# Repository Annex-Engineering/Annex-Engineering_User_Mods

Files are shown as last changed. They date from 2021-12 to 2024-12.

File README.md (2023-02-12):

# Annex Engineering - User Mods

This repo hosts mods created by the development team and end users of the Annex Engineering line of printers, extruders and other misc projects. Please follow the folder hierarchy described below when creating a pull request

This repo may also host mods created for other printers, by the annex development team. They are filed in the "Printers/Other_Printers" folder

## Folder Hierarchy:
 -  / printer / user_name-mod_name / STLs /
 -  / printer / user_name-mod_name / CAD /
 -  / printer / user_name-mod_name / Images /
 -  / printer / user_name-mod_name / README.md

### Notes: 
 - README.md should include any pictures, boms, instructions, etc
 - CAD should include all steps, parasolids, solidworks files, or other cad files
 - STLs should include any and all STLs required
 - Images should include all required pictures, videos, etc

Our discord server can be found here: 

Join me on Discord (https://discord.gg/MzTR3zE)

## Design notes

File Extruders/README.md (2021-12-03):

# Annex Engineering - User Mods - Extruders

This repo hosts mods created by end users of the Annex Engineering line of Extruders. Please follow the folder hierarchy described on the main README.md when creating a pull request

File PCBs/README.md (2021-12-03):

# Annex Engineering - User Mods - PCBs

This repo hosts mods created by end users of the Annex Engineering line of PCBs. Please follow the folder hierarchy described on the main README.md when creating a pull request

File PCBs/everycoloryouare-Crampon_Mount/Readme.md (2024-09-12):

# Nozzle Mount for Crampon

A Crampon mount that attaches to the hotend and positions the accelerometer at the nozzle tip position. The standard Crampon mount provided on the [Annex Engineering PCB GitHub](https://github.com/Annex-Engineering/Annex_Engineering_PCBs/tree/master/crampon/Clampon_Mounting_Bracket/) is too wide to fit between the part cooling fans on a K3 and has the accelerometer offset from the nozzle. This version fixes those issues.

Two versions for the bottom printed part are available for USB cables with 6mm and 8mm thick housing on the connector.

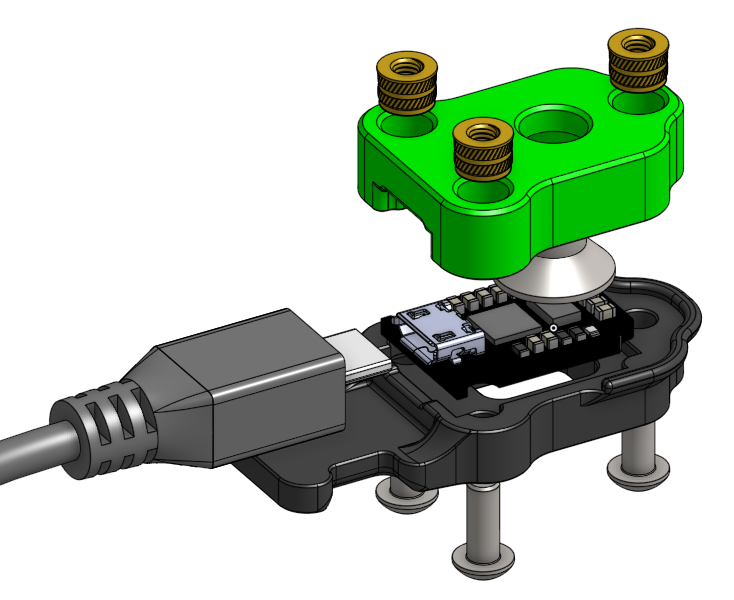
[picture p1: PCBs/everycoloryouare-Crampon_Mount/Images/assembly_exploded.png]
Exploded


## Goals

- Positions the ADXL345 accelerometer at the nozzle tip
- Minimizes weight while still being easy to install (work in progress)
- Fits on the K3 carriage without hitting the part cooling fan ducts or Beacon probe
- Works with 6mm and 8mm thick USB cables

## BOM

- Sources for all items can be found in the Annex [sourcing guide](https://docs.google.com/spreadsheets/d/1O3eyVuQ6M4F03MJSDs4Z71_XyNjXL5HFTZr1jsaAtRc/htmlview#) for the K3 or at the official Annex Stores ([US](https://store.annex.engineering/), [EU](https://annex-engineering.eu/))

| Item | Qty Required |
| --- | --- |
| Crampon PCB | 1 |
| M6 x 10mm or 12mm Flat Head (included with Crampon) | 1 |
| M3 x 8mm SHCS or BHCS | 3 |
| M3 x 5mm Dia x 4mm Length Heat Set Insert | 3 |
| Micro USB Cable with 6mm or 8mm thick housing | 1 |
| Cable Tie | 1 |

## Notes

Relative position of ADXL345 chip (highlighted) and nozzle mounting bolt:

| This Version | Standard | Legacy (Minimal) |
| --- | --- | --- |
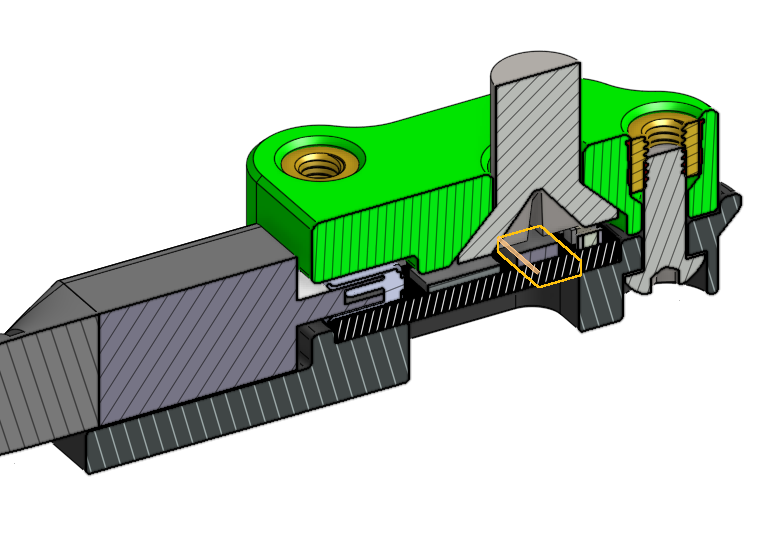
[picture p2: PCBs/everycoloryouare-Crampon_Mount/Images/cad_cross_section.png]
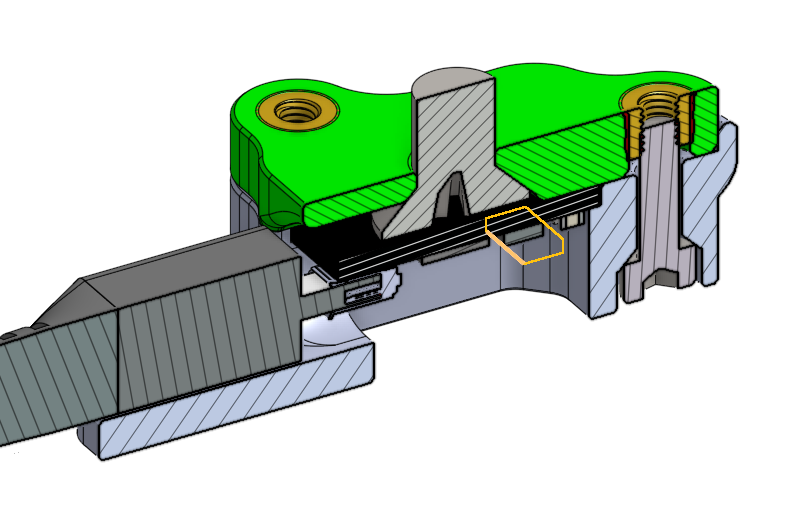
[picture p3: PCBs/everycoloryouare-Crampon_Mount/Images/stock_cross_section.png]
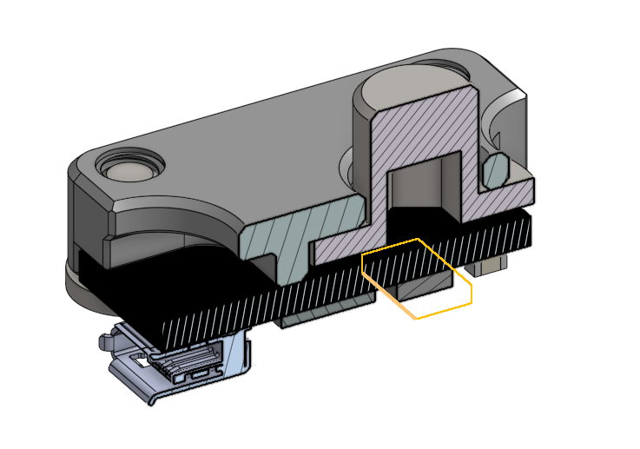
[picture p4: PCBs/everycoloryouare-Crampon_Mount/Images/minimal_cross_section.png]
|  |  |  |

- The PCB recess in the bottom printed part is 1.4mm, so the Crampon should sit 0.2 above the lip so that it is in contact with the top printed part.

## Assembly

1. Insert three M3 heat set inserts into the top printed part.
2. Insert Crampon PCB into the bottom printed part.
3. Attach USB cable to Crampon and zip-tie USB cable to the strain relief tab on the bottom printed part.
4. Remove nozzle from the hotend.
5. Attach the top printed part into the hotend thread using a M8 flat head bolt.
6. Attach the bottom printed part using three M3 bolts.

## Print Settings

- Nozzle Size: 0.4mm or 0.5mm
- Material: ABS, ASA, or PLA
- Layer Height: 0.2mm
- Infill Percentage: 40%
- Wall Count: 4
- Solid Top/Bottom Layers: 5

Print with imported orientation and no shrink compensation for ABS, ASA, or PLA.

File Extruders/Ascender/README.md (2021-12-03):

# Annex Engineering - User Mods - Extruder - Ascender

This repo hosts mods created by end users of the Annex Engineering - Ascender Extruder. Please follow the folder hierarchy described on the main README.md when creating a pull request

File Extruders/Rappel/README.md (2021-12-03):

# Annex Engineering - User Mods - Extruder - Rappel

This repo hosts mods created by end users of the Annex Engineering - Rappel Extruder. Please follow the folder hierarchy described on the main README.md when creating a pull request

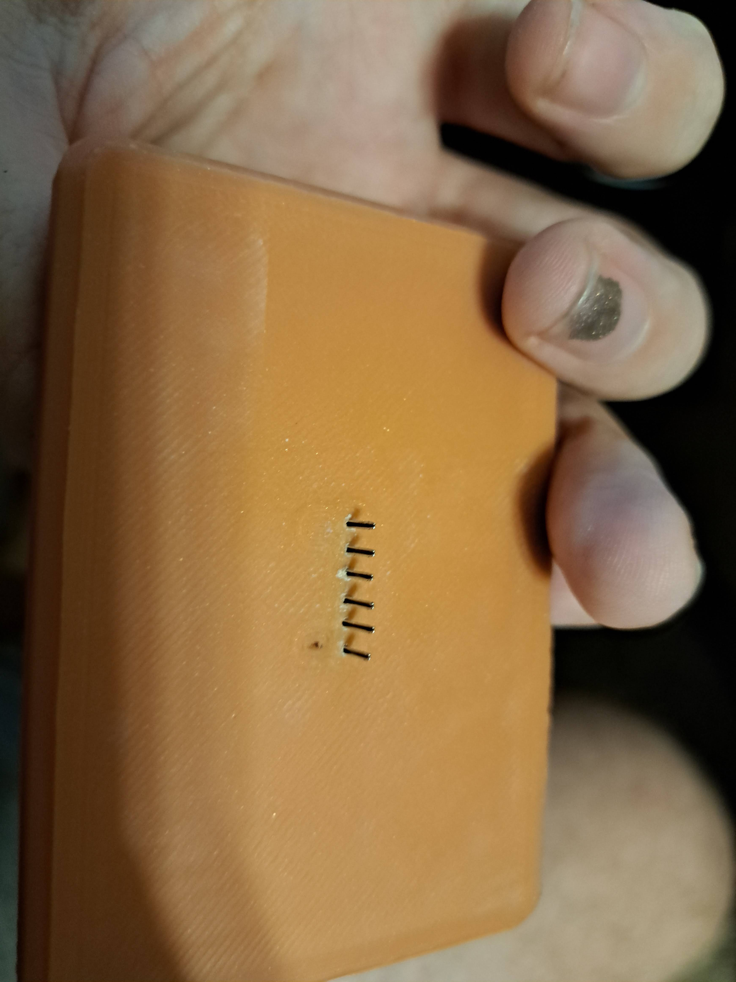
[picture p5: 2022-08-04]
Printers/K3/kirby-ADXL-headers-electronics-box-panel/Images/Front.jpg

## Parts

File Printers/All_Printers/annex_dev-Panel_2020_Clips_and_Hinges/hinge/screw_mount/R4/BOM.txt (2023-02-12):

Screw mount hinge BOM (per one hinge):
1x M5x40 SHCS or BHCS
1x M5 nut
2x M3x8 SHCS
2x M3 post assembly nut or T-nut
2x F695 bearing

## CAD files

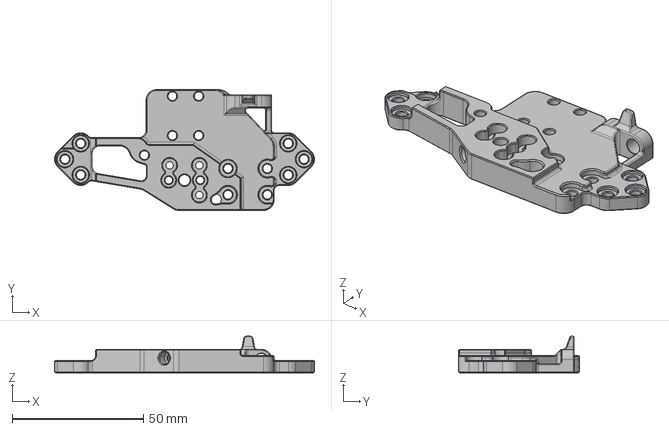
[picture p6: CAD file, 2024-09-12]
Printers/K3/everycoloryouare-K3rabiner_Micro_Plate/CAD/k3rabiner_sherpa_micro_mosqito_dragon_main_body_x1_rev2.step
99.0 x 46.0 x 13.9 mm

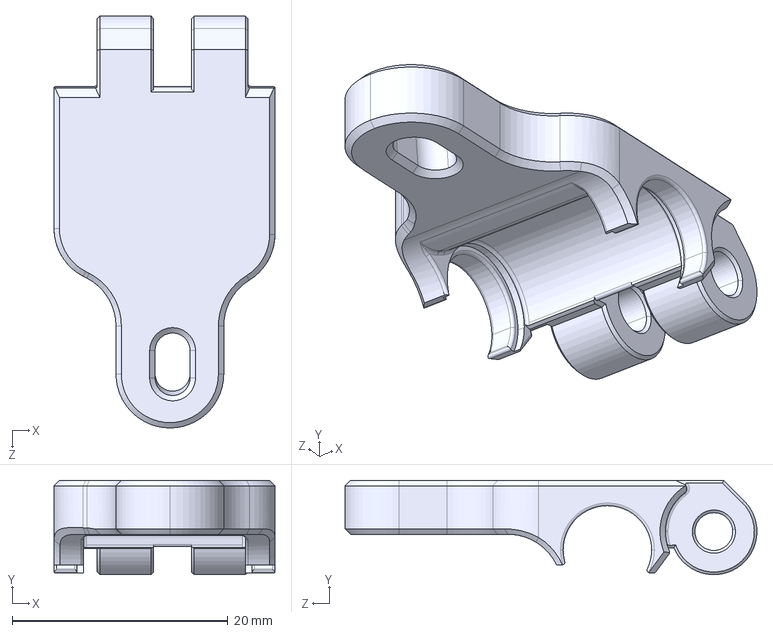
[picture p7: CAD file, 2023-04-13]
Extruders/Ascender/churls-Ball_bearing_latch/CAD/mr85_ascender_latch.STEP
20.5 x 8.74 x 38.2 mm

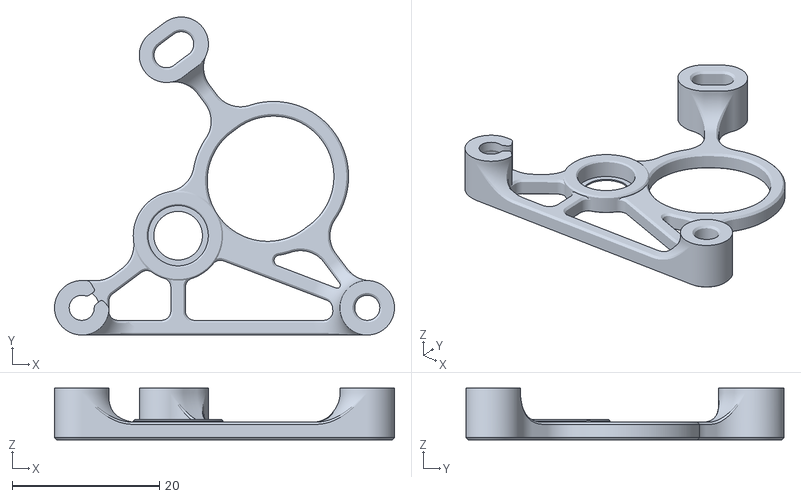
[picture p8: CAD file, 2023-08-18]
Extruders/Sherpa_Micro/Extruder_Mods/Churls_Fixed_Idler_Micro/STLs/Bondtech RIDGA V2/Sherpa_micro_housing_rear_0.2LH.STL
46.2 x 43.2 x 7.00

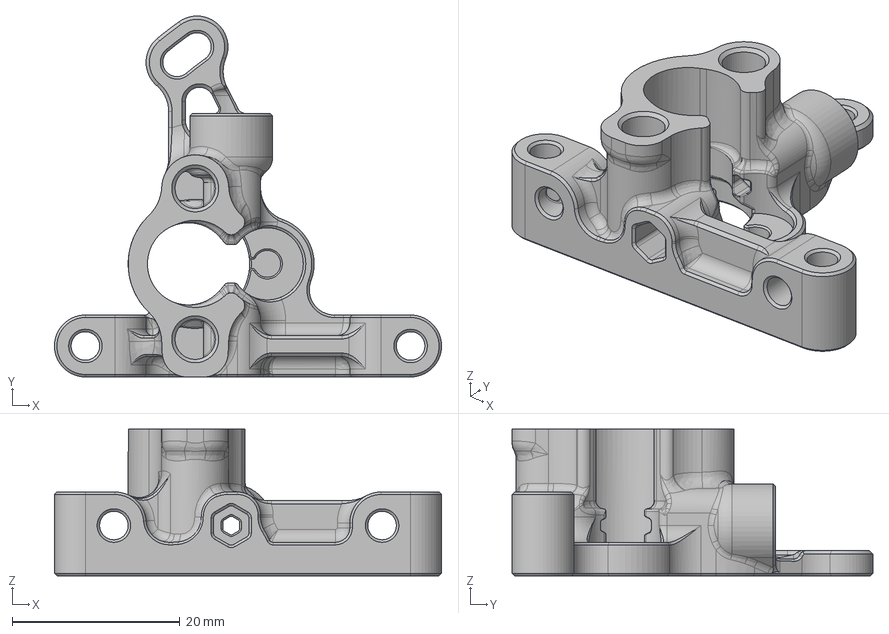
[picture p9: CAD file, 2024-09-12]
Extruders/Sherpa_Micro/Extruder_Mods/everycoloryouare-Fixed_Idler_Micro_and_Collet/CAD/fixed_idler_housing_core_collet_x1_rev2.step
46.2 x 43.1 x 17.5 mm

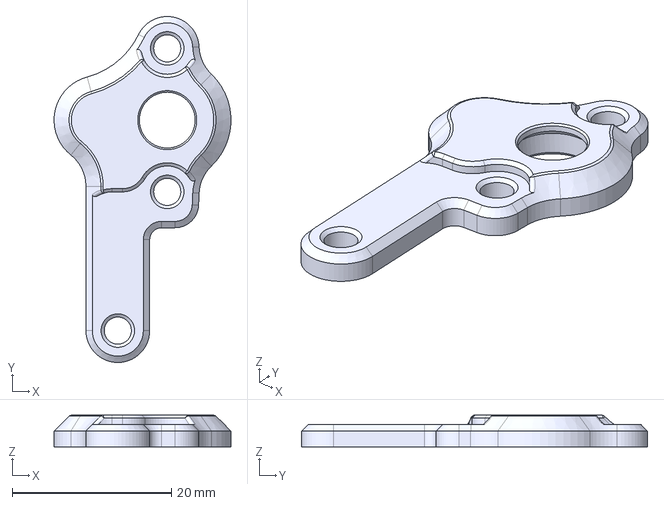
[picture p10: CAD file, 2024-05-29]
Extruders/Sherpa_Micro/Extruder_Mods/everycoloryouare-Fixed_Idler_Micro_and_Collet/CAD/mirrored/fixed_idiler_housing_front_k_mirrored_x1_rev1.step
22.2 x 43.4 x 4.00 mm

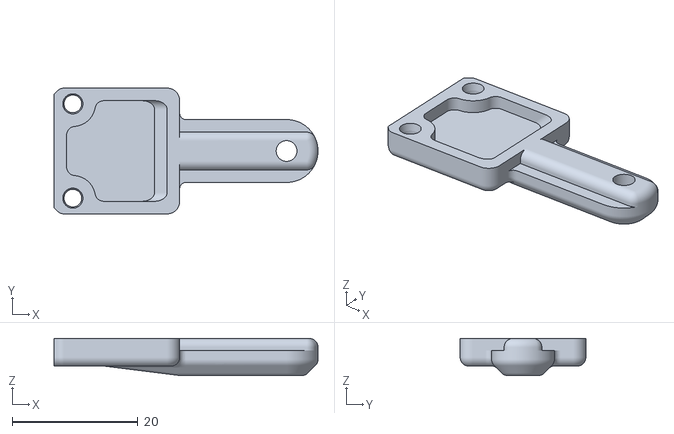
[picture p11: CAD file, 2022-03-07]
Extruders/Sherpa_Micro/Toolheads/Churls-Micro_Stiffy_E3/STLs/Optional/x_endstop_holder.STL
42.0 x 20.0 x 5.90

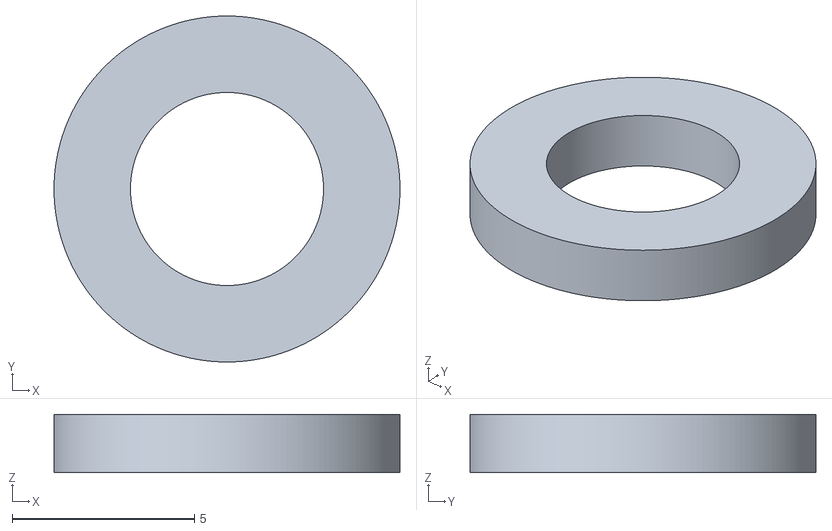
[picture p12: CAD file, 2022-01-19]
Extruders/Sherpa_Micro/Toolheads/Churls-Micro_Stiffy_E3/STLs/V_Roller_Spacer.STL
9.50 x 9.50 x 1.60

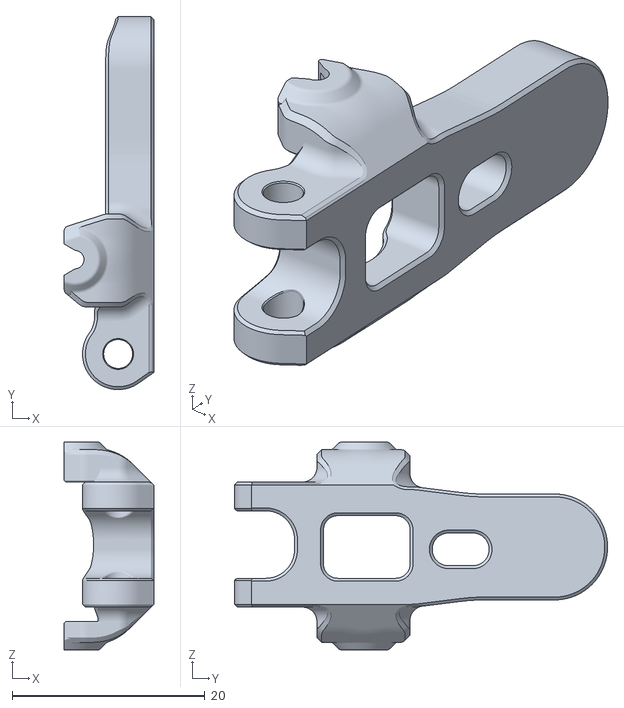
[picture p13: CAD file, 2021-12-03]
Extruders/Sherpa_Mini/Extruder_Mods/alch3my-4.6mm_mod/stls/sherpa_mini_release1 parts - idler_arm_long^housing_sherpa_mini_a3_r9c.stl
9.30 x 38.8 x 21.6

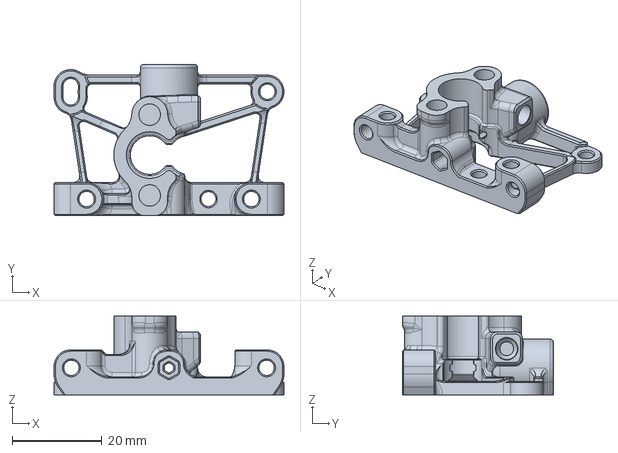
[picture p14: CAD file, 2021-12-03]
Extruders/Sherpa_Mini/Extruder_Mods/alch3my-Housing_Core_with_ECAS_coupler/housing_core_ECAS.step
51.2 x 33.7 x 17.5 mm

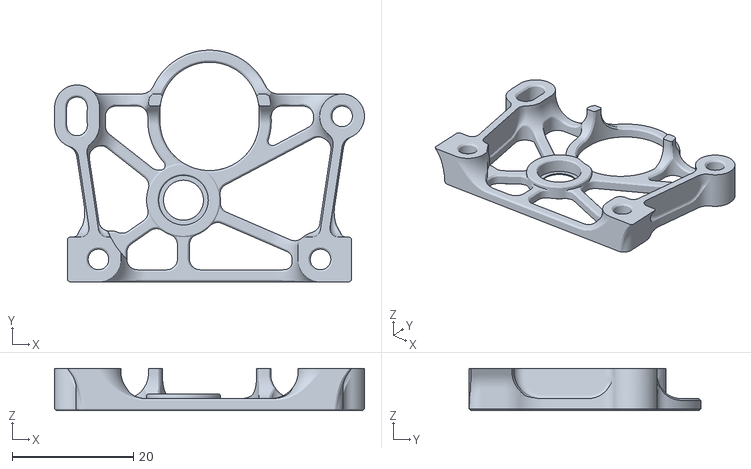
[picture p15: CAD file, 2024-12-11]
Extruders/Sherpa_Mini/Extruder_Mods/ChadwickTheCrab-4.6mm_Mod R2/STLs/housing_rear_nema14^housing_sherpa_mini_a3_r17_FDM.stl
51.2 x 38.3 x 7.00

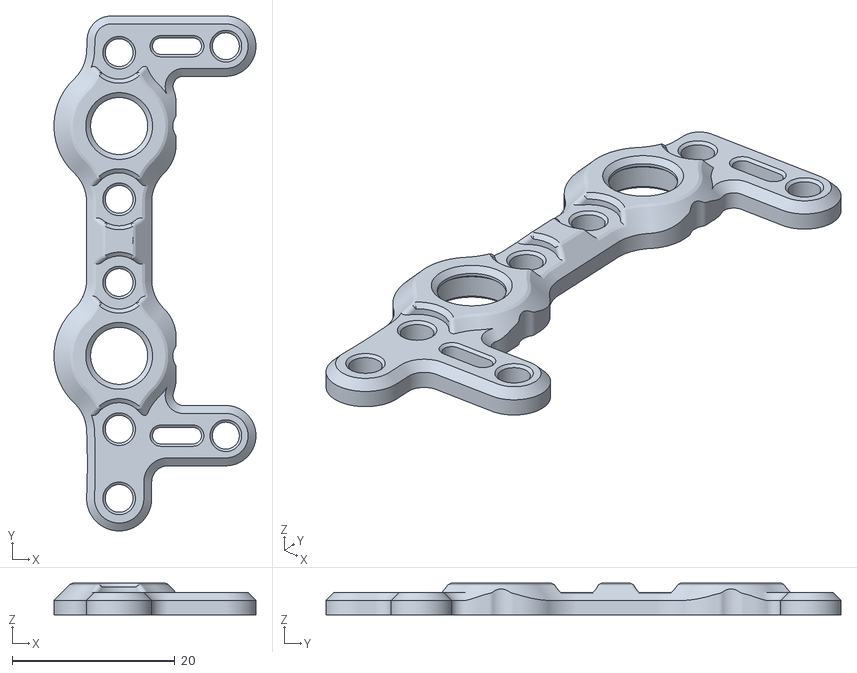
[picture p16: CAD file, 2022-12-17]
Extruders/Sherpa_Mini/Extruder_Mods/Churls-Double_Sherpa_Mini/STLs/housing_front_k.STL
24.8 x 63.2 x 3.90

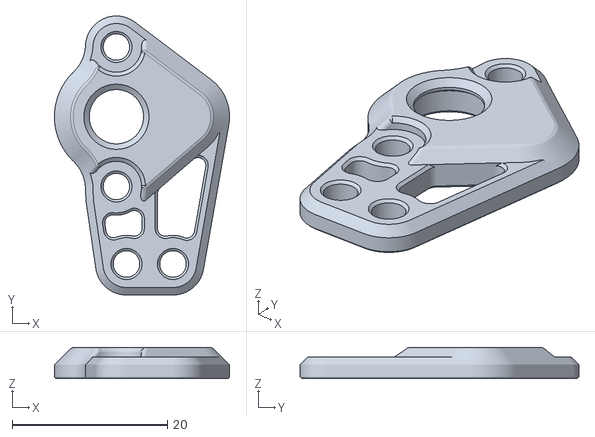
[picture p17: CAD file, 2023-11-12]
Extruders/Sherpa_Mini/Extruder_Mods/Churls-Fixed_Idler_Mini/STLs/Bondtech Gears/fixed_idler_housing_front_k2.STL
22.6 x 36.0 x 4.00

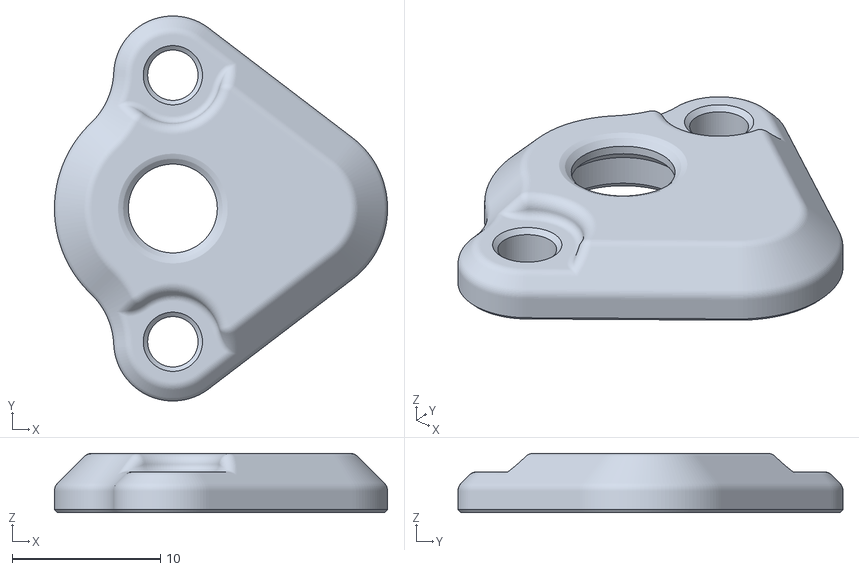
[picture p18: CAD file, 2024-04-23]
Extruders/Sherpa_Mini/Extruder_Mods/Churls-Fixed_Idler_Mini/STLs/Bondtech Gears/RIDGA V1/fixed_idler_mini_housing_front_btRIDGA.stl
22.5 x 26.0 x 4.00

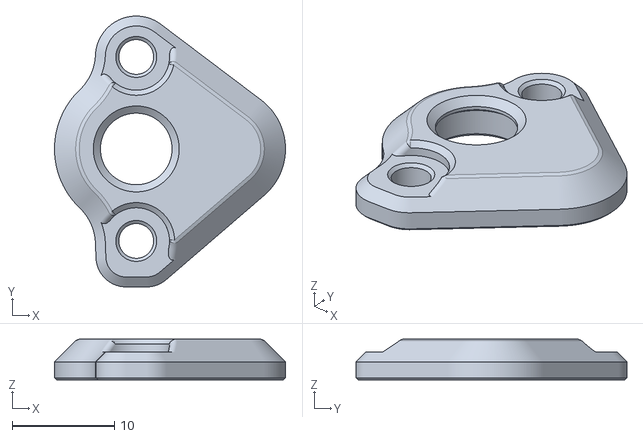
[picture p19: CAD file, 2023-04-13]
Extruders/Sherpa_Mini/Extruder_Mods/Churls-Fixed_Idler_Mini/STLs/Mellow vzRIDGA Gears/Sherpa_Housing_front.STL
22.6 x 26.5 x 4.00

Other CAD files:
Extruders/Sherpa_Micro/Extruder_Mods/everycoloryouare-Fixed_Idler_Micro_and_Collet/STLs/mirrored/[a]_fixed_idler_housing front_k_mirrored_x1_rev1.stl
Extruders/Sherpa_Mini/Extruder_Mods/Churls-Mini_RIDGA/STLs/Bondtech RIDGA Gears/RIDGA V1/4x7x2.5 Bearings/RIDGA_Sherpa_housing_front_4x7x2.5_BRG.STL
Extruders/Sherpa_Mini/Extruder_Mods/Churls-Mini_RIDGA/STLs/Bondtech RIDGA Gears/RIDGA V1/4x8x3 Bearings/RIDGA_sherpa_mini_housing_front_4x8x3_BRG.STL
Extruders/Sherpa_Micro/Extruder_Mods/Churls_Fixed_Idler_Micro/STLs/Bondtech RIDGA V1/Sherpa_micro_housing_front.STL
Extruders/Sherpa_Micro/Extruder_Mods/Churls_Fixed_Idler_Micro/STLs/Bondtech RIDGA V1/Sherpa_micro_housing_rear.STL
Extruders/Sherpa_Micro/Extruder_Mods/Churls_Fixed_Idler_Micro/STLs/Bondtech RIDGA V2/Sherpa_housing_front.STL
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

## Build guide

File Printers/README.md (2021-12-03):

# Annex Engineering - User Mods - Printers

This repo hosts mods created by end users of the Annex Engineering line of printers. Please follow the folder hierarchy described on the main README.md when creating a pull request

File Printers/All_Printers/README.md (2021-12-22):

# Annex Engineering - User Mods - Printer - Any ANNEX Engineering Printer

This repo hosts mods created by end users of Annex Engineering printers. Please follow the folder hierarchy described on the main README.md when creating a pull request

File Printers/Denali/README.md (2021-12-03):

# Annex Engineering - User Mods - Printer - Denali

This repo hosts mods created by end users of the Annex Engineering - Denali Printer. Please follow the folder hierarchy described on the main README.md when creating a pull request

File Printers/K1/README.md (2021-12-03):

# Annex Engineering - User Mods - Printer - K1

This repo hosts mods created by end users of the Annex Engineering - K1 Printer. Please follow the folder hierarchy described on the main README.md when creating a pull request

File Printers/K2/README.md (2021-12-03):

# Annex Engineering - User Mods - Printer - K2

This repo hosts mods created by end users of the Annex Engineering - K2 Printer. Please follow the folder hierarchy described on the main README.md when creating a pull request

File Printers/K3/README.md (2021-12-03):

# Annex Engineering - User Mods - Printer - K3

This repo hosts mods created by end users of the Annex Engineering - K3 Printer. Please follow the folder hierarchy described on the main README.md when creating a pull request

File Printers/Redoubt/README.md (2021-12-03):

# Annex Engineering - User Mods - Printer - Redoubt

This repo hosts mods created by end users of the Annex Engineering - Redoubt Printer. Please follow the folder hierarchy described on the main README.md when creating a pull request

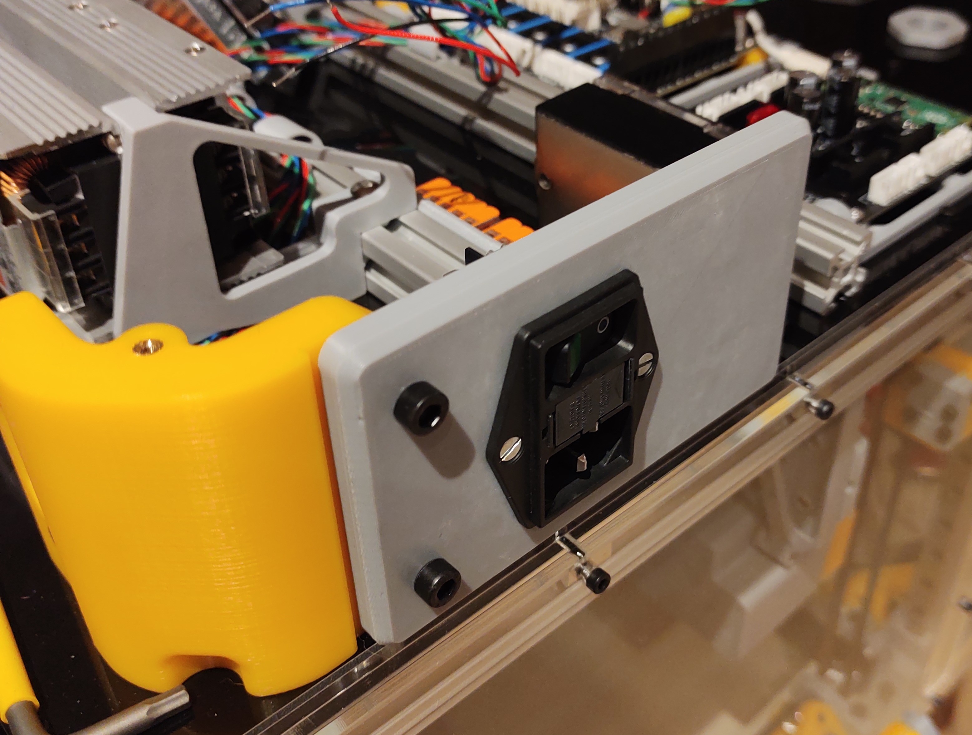
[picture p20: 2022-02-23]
Printers/All_Printers/Pringineer-Ebox_Plate_Schurter_DD11/Images/Schurter_Inlet_DD11_front.jpg

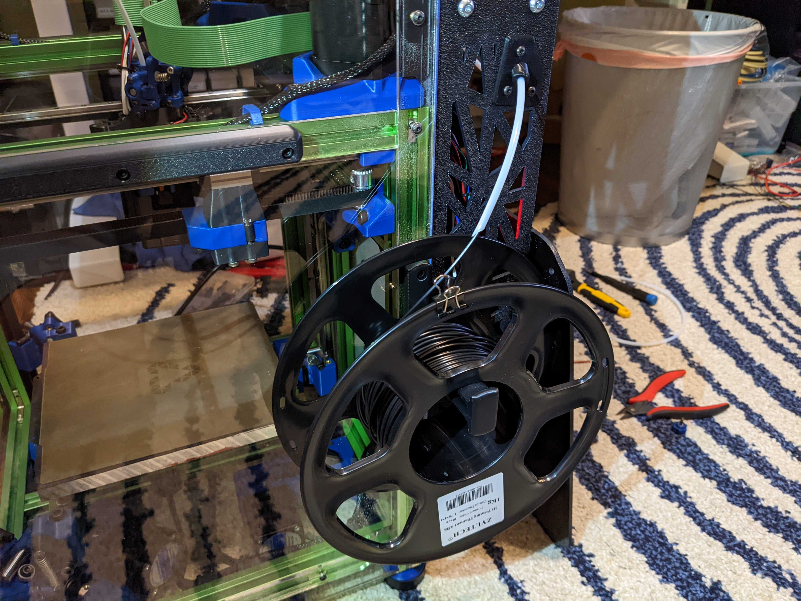
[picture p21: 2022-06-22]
Printers/K3/long-right_side_PTFE_tube_guide/Images/sideview.jpg

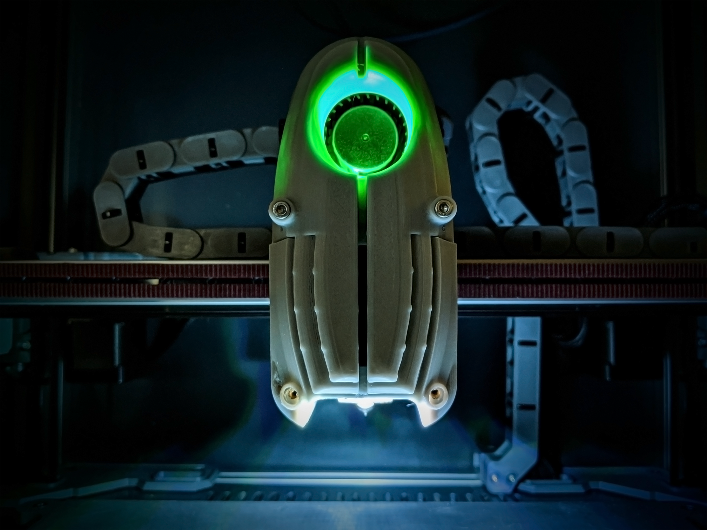
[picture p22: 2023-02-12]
Printers/Non_Annex_Printers/VORON_Printers/VORON_Afterburner_Beta1/annex_dev-(M)ORON_Afterburner_Front_Cover/Images/Action.png

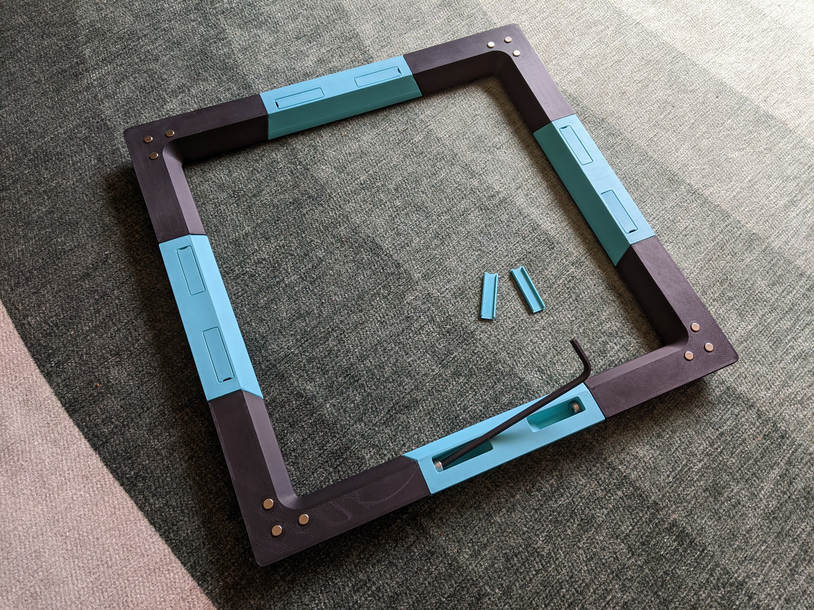
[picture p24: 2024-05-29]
Printers/K3/everycoloryouare-M5_Tophat/Images/printed_bottom.jpg

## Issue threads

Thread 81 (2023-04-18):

housing front version without 5th screw

Horstelin, 2023-04-18:
Hey, could you design/upload a version of the housing_front(double) that does not have the additional mounting hole? The current version is not compatible with the dragon burner and other toolheads.

Otherwise: great design!

Closed 2023-10-07.

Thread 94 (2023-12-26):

Potentially out of date STL or incorrect readme for 2.4 reinforced gantry

sqwoobler, 2023-12-26:
The readme for v3 of the reinforced gantry shows a heat set insert in the z tensioner (to remove the spacer when stuck),  the space for this insert seems to be missing from the STL (below). Not sure if this is a mistake in documentation and the design changed, or perhaps a STL was not updated with the readme.

https://github.com/Annex-Engineering/Annex-Engineering_User_Mods/blob/6e3e89a6c8ef50cbd4bdfff7f6232c564b06ec55/Printers/Non_Annex_Printers/VORON_Printers/VORON_V2dot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

sqwoobler, 2024-01-05:
Mistake on my end.

Closed 2024-01-05.

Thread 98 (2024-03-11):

Newer revisions of stealthburner x carriage mount are shorter than they should be

KianSajjadi, 2024-03-11:
The 3rd revision of the mount had a change in the mounting height of the beacon causing the rapido nozzle to crash into the bed. Compare these two links with the same rev3 label:
https://github.com/Annex-Engineering/Annex-Engineering_User_Mods/blob/17229e6174104a9cb21d33a0cb7ea2c23882a710/Printers/Non_Annex_Printers/VORON_Printers/VORON_V2dot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
https://github.com/Annex-Engineering/Annex-Engineering_User_Mods/blob/4cb96361011dc72d3039e8c95225dbc5614b5aa5/Printers/Non_Annex_Printers/VORON_Printers/VORON_V2dot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

The first link has the correct beacon mounting height whereas the second link changes the mounting height of the beacon causing nozzle crashes. I think there should be a second version in the STLs where the original mounting height of the beacon is included for rapido users.

Closed 2024-05-29.

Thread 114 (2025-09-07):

Stealthburer Beacon X carriage: offset documentation

system-dsn, 2025-09-07:
Thanks for providing this carriage!

I haven't been able to find a definitive source for the nozzle-to-probe offsets so I went to various CAD models to measure:

- Beacon sensor to "nose" distance: 8.5mm
- "Nose" of Beacon to X carriage hotend mounting surface: 1.0mm
- Stealthburner Revo Voron mount, mounting surface to nozzle: 14.6mm

So the y offset should be 8.5+1.0+14.6=24.1mm.

If my measurements are right then it might be helpful for others to document this in the README:

```
[beacon]
x_offset: 0
y_offset: 24.1
```

(This is only for the Revo Voron with the normal profile Beacon RevH. Not sure about other Beacon/hotend combinations.)

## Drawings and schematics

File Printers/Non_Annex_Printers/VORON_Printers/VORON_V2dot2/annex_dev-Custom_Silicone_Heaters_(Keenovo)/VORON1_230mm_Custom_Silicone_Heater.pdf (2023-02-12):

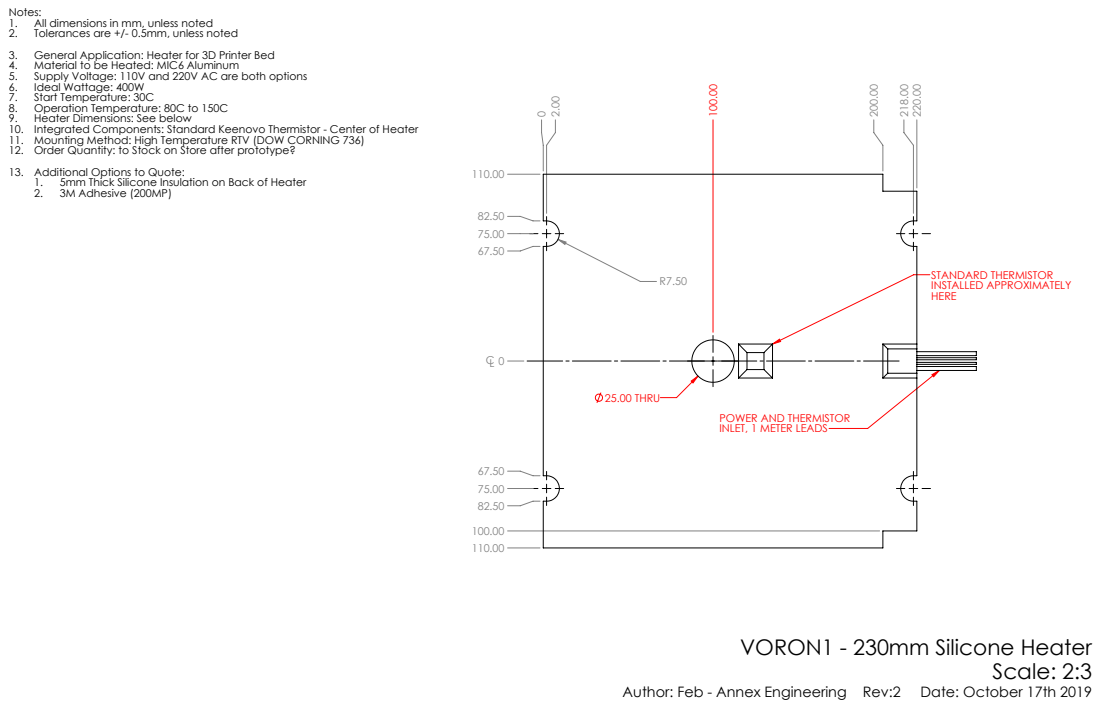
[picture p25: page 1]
25.00 THRU; STANDARD THERMISTOR INSTALLED APPROXIMATELY HERE; VORON1 - 230mm Silicone Heater Scale: 2:3

Notes:
1. All dimensions in mm, unless noted
2. Tolerances are +/- 0.5mm, unless noted
3. General Application: Heater for 3D Printer Bed
4. Material to be Heated: MIC6 Aluminum
5. Supply Voltage: 110V and 220V AC are both options
6. Ideal Wattage: 400W
7. Start Temperature: 30C
8. Operation Temperature: 80C to 150C
9. Heater Dimensions: See below
10. Integrated Components: Standard Keenovo Thermistor - Center of Heater
11. Mounting Method: High Temperature RTV (DOW CORNING 736)
12. Order Quantity: to Stock on Store after prototype?
13. Additional Options to Quote:
1. 5mm Thick Silicone Insulation on Back of Heater
2. 3M Adhesive (200MP)

POWER AND THERMISTOR
INLET, 1 METER LEADS

Author: Feb - Annex Engineering Rev:2 Date: October 17th 2019

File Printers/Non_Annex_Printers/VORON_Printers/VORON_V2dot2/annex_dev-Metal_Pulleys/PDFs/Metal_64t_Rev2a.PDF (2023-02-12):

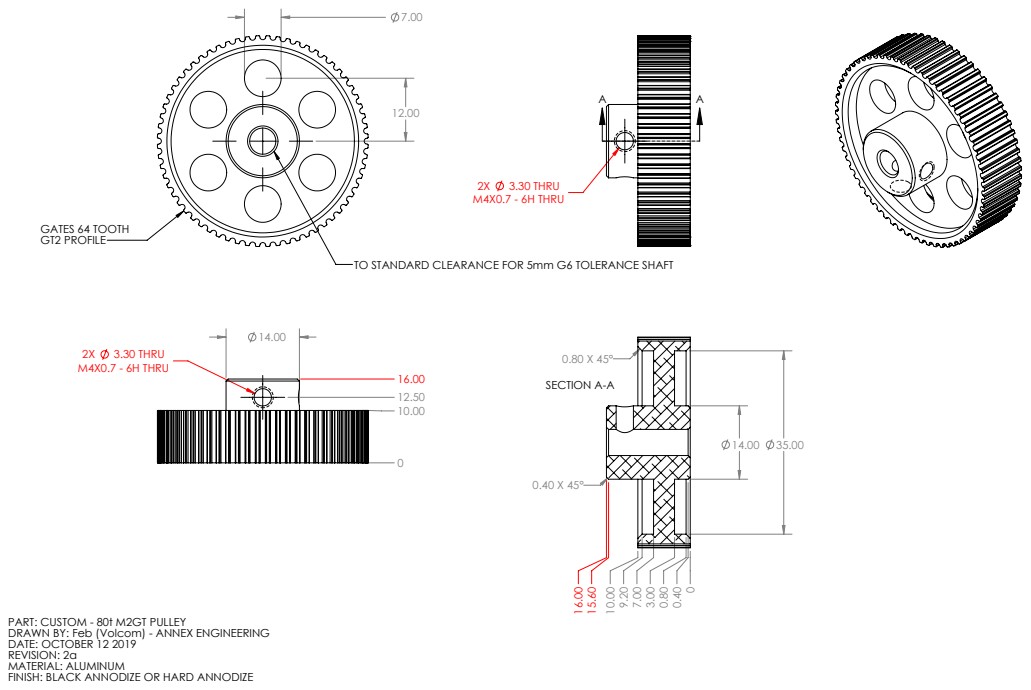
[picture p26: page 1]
GATES 64 TOOTH GT2 PROFILE; 3.30 THRU; M4X0.7 - 6H THRU; SECTION A-A

TO STANDARD CLEARANCE FOR 5mm G6 TOLERANCE SHAFT

PART: CUSTOM - 80t M2GT PULLEY
DRAWN BY: Feb (Volcom) - ANNEX ENGINEERING
DATE: OCTOBER 12 2019
REVISION: 2a
MATERIAL: ALUMINUM
FINISH: BLACK ANNODIZE OR HARD ANNODIZE

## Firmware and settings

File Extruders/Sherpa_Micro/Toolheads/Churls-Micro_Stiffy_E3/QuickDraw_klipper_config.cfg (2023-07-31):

# Download Dalegaard's xz dockable probe module to `~/klipper/klippy/extras/ folder on klipper host as `xz_dockable_probe.py`:
#	A copy of this module has been placed in this repository with Dalegaard's permission. You can download it with these SSH commands:
#		cd ~/klipper/klippy/extras/
#		wget https://raw.githubusercontent.com/churls5495/Annex-Engineering_User_Mods/main/Extruders/Sherpa_Mini/Toolheads/Churls-Stiffy_E3/xz_dockable_probe.py
#		cd ../..
#		echo "klippy/extras/xz_dockable_probe.py" >> .git/info/exclude
#		systemctl restart klipper
#
#	It can also be found here: https://gist.github.com/dalegaard/3f1b8695275a15b1888119304d79b88d
#
#	This module provides additional klipper commands:
#		probe_attach		# attaches probe to toolhead
#		probe_detach		# detaches probe from toolhead
#		probe_lock		# disables auto docking functionality
#		probe_unlock		# reenables auto docking functionality
#		G28 lock_probe=1	# disables auto docking after homing
#		probe_detach force=1	# unlock_probe + probe_detach
#
#	Example:
#		G28 lock_probe=1	# Home XY, attach probe, home Z with probe on bed, hold probe (rather than auto docking immediately as G28 alone would)
#		bed_mesh_calibrate	# generate mesh
#		probe_detach force=1 	# unlocks and docks

# Modifications to printer.cfg
[stepper_z]
endstop_pin: probe:z_virtual_endstop # was ^PC2
#position_endstop: 0.0      	# comment out or delete this line

[stepper_x]
position_max: 265		# more X travel to enable probing along X=225. This is why the upper right v-roller bolt is flipped.

# Additions to printer.cfg
[xz_dockable_probe]
dock_pin: ^PC2			# stock Z endstop pin
dock_x: 17			# X position of nozzle that aligns toolhead and probe magnets
park_delta_x: -15		# X travel to retrieve probe from dock (relative to dock_x)
detach_delta_x: 15		# X travel to detach probe from toolhead (relative to dock_x)
z_hop: 20			# Z travel to clear dock
home_xy_position: 148.5,116.72	# probe point for homing (bed center - probe offset)
#hook_commands: False 		# optional setting to disable the auto attach/detach features. Default is True

[probe]
pin:^PC14			# pin wired to QuickDraw
x_offset: -30
y_offset: 0.78
z_offset: 7.55			# calibrate with probe_calibrate command
samples: 3
sample_retract_dist: 10
samples_result: median
samples_tolerance: 0.01
samples_tolerance_retries: 3
speed: 3
lift_speed: 15

[bed_mesh]
mesh_min: 5,5
mesh_max: 230,230
horizontal_move_z: 10
probe_count: 5,5
fade_start: 0.4
fade_end: 2
bicubic_tension: 0.1
speed: 200
algorithm: bicubic
relative_reference_index: 12

[gcode_macro clear_Z_offset]
description: reset Z offset to zero
gcode:
    SET_GCODE_OFFSET Z=0 

[gcode_macro probe_prep]
description: Heat bed and attach probe
gcode:
    {% set BED_TEMP = params.BED_TEMP|default(60) %}
    M190 S{BED_TEMP}
    G28 lock_probe=1
    
[gcode_macro dock_probe]
gcode:
    probe_detach force=1

[gcode_macro mesh]
description: Heat bed, attach probe, home, mesh, detach probe
gcode:
    {% set BED_TEMP = params.BED_TEMP|default(60) %}
    M190 S{BED_TEMP}
    G28 lock_probe=1
    bed_mesh_calibrate
    probe_detach force=1


[screws_tilt_adjust]
screw1: 236.5,202.5 
screw1_name: rear right 
screw2: 66.5,202.5 
screw2_name: rear left 
screw3: 66.5,32.5
screw3_name: front left
screw4: 236.5,32.5
screw4_name: front right
speed: 200
horizontal_move_z: 10
screw_thread: CW-M4

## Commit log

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2021-12-13 Magprobe for Switchwire MGN12H README
    Update broken images and broken link to the probe housing.
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2022-02-08 raised lowest point of duct tips 1mm.
    ducts were hitting bed before nozzle on some assemblies. this provides more clearance. There should be 0.75mm of clearance on stock setups now.
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2022-02-10 Add K3 Klipper Screen mod
    This adds a door mounted 3.5" KlipperScreen driven display.
    [back_case.stl, front_case.stl, hinge_arm.stl]
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2022-02-10 Corrections to quickdraw cfg
    [QuickDraw_klipper_config.cfg]
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2022-02-10 CAD and Quickdraw updates for Stiffy and Chubby
    - Raised lowest points of stiffy and chubby
    - updated cad with changes
    - added quickdraw documentation to chubby
    [Chubby.x_t, QuickDraw_klipper_config.cfg, Stiffy.x_t]
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2022-02-16 Added 4020 Fan support to Stiffy
    new 4020 fan brace STLs
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2022-02-21 UHP bracket mod
    Modded UHP bracket for dual PSU
    [UHP_mod_bracket (mirrored).stl, UHP_mod_bracket v7.f3d, UHP_mod_bracket v7.step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]
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2022-03-07 updated QD dock STL, added adjustable X endstop
    [x_endstop_holder.STL]
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2022-03-07 Adding QD macros to stiffy and chubby
    [QuickDraw_klipper_config.cfg]
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2022-03-12 Set correct orientation
    [led-profile-mount.stl]
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2022-04-18 Adds Stiffy for Ender-3 V2
    [Stiffy_Ender-3_V2.stl]
2022-04-20 Fix led mount issue with height of certain part
    [led-profile-mount.stl]
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2022-05-25 folder restructuring for e3v2 for stiffy and chubby
    [Chubby_E3V2.stl, Stiffy_E3V2.stl]
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2022-06-18 Stiffy gets Sherpa Micro Version
    [Stiffy_micro.STEP, Stiffy_micro.x_t]
2022-06-19 Created Micro Stiffy Toolhead
    [Micro_Stiffy.x_t, QuickDraw_klipper_config.cfg, V_Roller_Spacer.STL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]
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2022-07-10 Add files via upload
    new models with updated names
    [probe_Body.stl, probe_pin_v3.stl]
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2022-07-11 Add files via upload
    updated to v4. parts going through testing.
    [pin_v4.stl, probe body_v4.stl]
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2022-08-03 Added two mods: ADXL jumper blanking box, and push-fit PTFE connector
    See readmes for each file.
    [Electronics_Box_Blanking_Plate_ADXL_headers.SLDPRT, Electronics_Box_Blanking_Plate_ADXL_headers.STL, Inner_Cap.STL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]
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2022-08-29 OV5640 Camera (100 degree) Mount
    Mount for 100 degree OV5640 Camera that sits in the back right corner.
    [2020_extrusion_cable_cover.stl, OV5640_Mount_StockScrews_10degree.stl, OV5640_Mount_StockScrews_15degree.stl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]
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2022-09-06 Added cable tie post and improved Quickdraw mounting
    [Stiffy_micro.STEP]
2022-09-07 Micro Stiffy Updates
    better QD magnet retention
    cable post
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2022-09-08 Fix Clearances
    [Volcomosq spacer v3.step, Volcomosq_Spacer.stl.3mf]
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2022-09-08 moved stiffy fan braces to optional folder
2022-09-25 Adding Neptune 2 version of the Stiffy
    [Stiffy_Neptune2.step]
2022-10-16 add K3 Waveshare Screen Mount
    Wwavershare 7.9" Screen mount for the K3, based on PRZY's K3+ Mount.
    [LCD_FRAME_K3_STANDARD.stl]
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2022-12-17 updated micro stiffy cad
    [Micro_Stiffy.x_t]
2022-12-17 deleted magnet retention features
    they didn't work.
    [Micro_Stiffy.x_t, Micro_Stiffy_no_post.x_t]
2023-01-13 Metal motor mount for K3
    Modified from released K3 CADS
    [Metal_XY_Motor_Mount.step]
2023-02-03 Chubby - QD simplification
    use glue and run wires down the side of the magnets rather than sandwiching
    [Chubby.x_t]
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2023-03-17 added fixed gear sherpa variants
2023-03-19 Pi Camera V3 Mount for K3 by Long
    [Pi Cam 3 Mount - Lens Cover - 12.4mm Lens.stl, Pi Cam 3 Mount - Mount - 15 degree down.stl, Pi Cam 3 Mount - Mount - 25 degree down.stl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]
2023-03-20 Upload K3 DFA Carabiner mount mod
    Carabiner mount for DFA on a K3 with full clearance
    [K3_DFA_Carabiner_Mount.step, K3_DFA_Carabiner_Mount.stl]
2023-03-24 added sherpa fixed idler CAD
    [RIDGA_Sherpa_Mini_housing_core.STEP, RIDGA_Sherpa_Mini_housing_core.x_t, Sherpa_micro_fixed_idler_housing_core.STEP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]
2023-03-24 added fixed gear housing front CAD
    [Sherpa_fixed_idler_housing_front_k.STEP]
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2023-03-25 added Beacon probe specific K3 nozzle wiper parts
    [Beacon_NozzleWiper.step, Nozzle_Wiper_Arm_Beacon.stl, Nozzle_Wiper_Base_Beacon.stl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]
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2023-03-27 Added ridga and fixed idler CAD
    [RIDGA_Sherpa_Micro_Housing_Core.STEP, RIDGA_Sherpa_Micro_Housing_Core.x_t, RIDGA_Sherpa_Micro_housing_front_k_4x8x3_bearing.STEP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]
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2023-04-01 Create Pi Cam 3 Mount - Lens Cover - 12.0mm Lens.stl
    Add 12.0 mm lens option
    [Pi Cam 3 Mount - Lens Cover - 12.0mm Lens.stl]
2023-04-01 small tweaks to CAD and Readme
    Added 12.0mm lens option in addition to the 12.4mm lens option for the picam v3 mount and updated the CAD.
    Added 2mm spacer for the right sided ptfe tube guide (only for people still on the old ebox).
    [PiCam3 Mount v40.f3d, PiCam3 Mount v40.step, PiCam3 Mount v43.f3d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]
2023-04-02 Move old K3 ebox usermods to Outdated folder
    [Electronics_Box_Blanking_Plate_ADXL_headers.SLDPRT, Electronics_Box_Blanking_Plate_ADXL_headers.STL, Electronics_Box_Blanking_Plate_Combo.step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]
2023-04-02 add Stiffy_E5_Dragonfly_BMS remix
    [Carabiner_mounting_Plate.stl, Stiffy3_E5_Dragonfly_BMS.step, Stiffy3_E5_Dragonfly_BMS.stl]
2023-04-03 Stiffy and Chubby get Beacon mounting
    [Chubby.STEP, Chubby.x_t, Stiffy.x_t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]
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2023-04-08 Added fixed idler sherpas for mellow vzRIDGA gears
    [Sherpa Housing_front.STL, Sherpa_micro_housing_front.STL, Sherpa_micro_housing_rear.STL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]
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2023-04-11 Upload LED Mod and tweak formatting
    Uploading the LED Mod I made for my K3 with tweaked mounts and flush door mount.
    Also fixed formatting in readme in my other mod
    [Diffuser_x3.stl, DoorSealAndLights.step, FrontMountAndDoorSeal.stl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]
2023-04-11 Update LEDHolder_x3.stl
    Fixed exported STL orientation
    [LEDHolder_x3.stl]
2023-04-12 Added Fixed idler Ascender
2023-04-13 Added MR85 fixed idler ascender mod
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2023-05-08 Added latest stiffy CAD
    [QuickDraw_klipper_config.cfg]
2023-06-02 Modified the frostbite duct, everything else is the same.
    [frostbite_duct_horizontal_STEP.step]
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2023-09-02 M5 Tophat Mod
    Added all relevant CAD, STLs, Images, and readme for the M5 tophat mod.
    [[a]_tophat_lid_structure_b_x4_rev1.step, [a]_tophat_lid_structure_c_x8_rev1.step, [a]_tophat_lid_structure_c_x8_rev1.stl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]
2023-09-02 Added Alignment Tools
    Added two alignment tools to the Printer/K3 folder, also fixed some spelling mistakes in the readme of the tophat mod.
    [mgn9c_m8-1.25_adapter_x1_rev1.step, mgn9c_m8-1.25_adapter_x1_rev1.stl, xy_pulley_shim_tool_x1_rev1.step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]
2023-09-04 Added Wago bed mount folder and files
    Also renamed tophat folder using underscore instead dash
    [[a]_tophat_lid_structure_b_x4_rev1.step, [a]_tophat_lid_structure_c_x8_rev1.step, [a]_tophat_lid_structure_c_x8_rev1.stl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]
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2023-09-05 Fixed chamber on carabiner mount top
    also updated images to have 8mm usb version so there is no intersection
    [crampon_mount_top_x1_rev1.step, crampon_mount_top_x1_rev1.stl]
2023-09-05 Fixed orientation of top stl
    [crampon_mount_top_x1_rev1.stl]
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2023-09-07 Fixed crampon mount readme
    Corrected bolt size for flat head screw
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2023-09-27 Added precompensated STLs
    Added 10 more versions of the tophat middle piece so that parts can be printed pre-comensated by different amounts, from 0.1 to 1.0%. Also updated Readme to reflect this change
    [[a]_tophat_lid_structure_b_x4_rev1.step]
2023-11-02 Adding Waveshare 4.3 bezel to mount to ebox
    [Waveshare_4_3_Screen Cover v2.3mf, Waveshare_4_3_Screen Cover v2.f3d]
2023-11-03 Moving to correct folder
    [Waveshare_4_3_Screen Cover v2.3mf, Waveshare_4_3_Screen Cover v2.f3d]
2023-11-03 Lan (CAT5) keystone as a connector for input shaping
    [Keystone Panel Mount v1.f3d, Panel Edge - Lan Keystone v5.3mf]
2023-11-11 Added sherpa mini with fixed idler, ridga, ECAS
    [Sherpa Housing - Sherpa_housing_front-1.STL, fixed_idler_housing_front.STL]
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2023-11-11 added sherpa fixed idler housing front k2
    [Sherpa Housing - Sherpa_housing_front-1.STL, fixed_idler_housing_front.STL, fixed_idler_housing_front_k2.STL]
2023-11-12 Update Beacon Mount
    Moved Beacon .285mm upwards, allowing all hotends to fit within beacons zone of 2.6-3mm from nozzle. Due to the voron revo being .285mm longer in vorons cad.
    [beacon_sb_xcarriage.STEP, x_carriage_left_x1_rev2.STL, x_carriage_left_x1_rev3.stl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]
2023-11-22 now with more hacks, i mean correctness
    [x_carriage_left_x1_rev3.stl, x_carriage_right_x1_rev3.stl]
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2023-12-06 Add inline filament sensor and sherpa mini and micro sensor mods
    [[a]_idler_arm_long_x1_rev1.STL, inline _filament_sensor_(5mm_collet).x_t, inline_filament_sensor_(6mm_collet).x_t]
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2024-02-12 Update Churls fixed Idler Sherpa Mini
    Change the RIDGA V1 to allow the use of the 6t motor. Also changed the body based on RC2
    [fixed_idler_housing_core_ECAS.STL, fixed_idler_housing_front.STL, fixed_idler_mini_housing_core_btRIDGA.stl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]
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2024-03-28 Added K3_Front_Base mod
    Mod to help seal chamber without having to affix foam to the Annex Door
    [K3_Front_Base.step, K3_Front_Base.stl]
2024-04-01 Revert "Added K3_Front_Base mod"
    This reverts commit 2b10d6ba944dcb310eb6a376a9fce12dfbbd0844.
    [K3_Front_Base.step, K3_Front_Base.stl]
2024-04-01 Added mods backpack logo and bottom seal
    Mods to help seal the air gaps in the bottom of the K3 and to add the Annex logo to the ebox like is shown in the edrawing
    [AnnexLogo.step, AnnexLogo.stl, BottomBackGasket.stl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]
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2024-04-19 Finalizing Mods
    Added Beacon Wiper, added misc K3 part mods, changed tophat folder stucture and instructions. Minor typo corrections
    [5.5mm_rail_xy_cross_rail_mount_mirror_x2_rev1.step, 5.5mm_rail_xy_cross_rail_mount_x2_rev1.step, [a]_mosquito_side_mount_modified_x1_rev1.step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]
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2024-05-11 improved tolerances
    Changed tolerances from 0.1 to 0.15 on most areas, fixed geometry mismatch on tophat corners due to incorrectly calculated tolerances
    [[a]_tophat_lid_center_x4_rev1.step, [a]_tophat_lid_center_x4_rev2.step, [a]_tophat_lid_cover_asa_x8_rev1.stl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]
2024-05-11 Added fixed idler sherpa micro with collet
    [[a]_fixed_idiler_housing front_k_mirrored_x1_rev1.stl, fixed_idiler_housing_front_k_mirrored_x1_rev1.step, fixed_idler_housing_core_x1_rev1.step]
2024-05-16 Added compensated step files
    Added compensated step in addition to uncompensated, added images of completed tophat, updated readme
    [[a]_tophat_lid_center_asa_x4_rev2.step, [a]_tophat_lid_center_x4_rev2.step, [a]_tophat_lid_cover_x8_rev2.step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]
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2024-06-12 Added eBox grommets
    2mm and 3mm panel versions of five grommet screw variants, and two sizes of grommet nuts with three clearance options each.
    [[a]_wiring_grommet_nut_25mm_0.1_x3_rev1.step, [a]_wiring_grommet_nut_25mm_0.2_x3_rev1.step, [a]_wiring_grommet_nut_25mm_x3_rev1.step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]
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2024-08-05 finalize naming, added 0.5mm clearance to some brackets
    [[a]_fixed_idiler_housing front_k_mirrored_x1_rev1.stl, [a]_fixed_idler_housing front_k_mirrored_x1_rev1.stl, carabiner_distribution_mounting_bracket_35_deg_x1_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]
2024-08-05 fixed geometry error on micro housing, updated name to reflect collet
    [fixed_idler_housing_core_collet_x1_rev2.step, fixed_idler_housing_core_x1_rev1.step]
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2024-08-13 Added fixed k3rabiner sherpa micro plate
    [k3rabiner_sherpa_micro_mosqito_dragon_main_body_x1_rev2.step, mirror_micro_front_plate_x1_rev2.step, mirror_micro_front_plate_x1_rev2.stl]
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2024-10-16 fixed folder name
    [BTT_MMB_Board_Tray.3mf, Canbus_Cord_Support.3mf, MMB_Board_Tray_Lid.3mf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]
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
